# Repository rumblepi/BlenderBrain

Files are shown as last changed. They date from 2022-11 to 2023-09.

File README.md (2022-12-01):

# BlenderBrain

A controller for continuous flow blending of Nitrox and Trimix gases for diving.
The controller uses two oxygen sensors (one after Helium injection and one after Oxygen injection) and from this computes the composition of the resulting gas.
The desired mix can be adjusted by the user and is then automatically controlled via two magnetic valves. Depending on the currently measured mix, the valves are kept open longer or shorter. For this, a PI controller is implemented.

## Hardware

In the 'Hardware' folder, the KiCad files for the PCB are stored. Due to availability issues, the current configuration of the controller uses an Atmega168 microcontroller, but if available an Atmega328P can and should be used. The board requires two power supplies, one 5V to supply the microcontroller and operational amplifiers and a 24V to supply the magnetic valves as well as the indicator lights.

The oxygen sensors are assumed to be common rebreather sensors, namely ones similar to the NRC D-05R sensor range. These sensors expose three pins, of which we will use two to measure the output voltage. These galvanic cell sensors are dependent current sources outputting a given current for a certain oxygen partial pressure. The sensor also contains a small temperature compensation circuit with a few resistors and an NTC element, such that it effectively outputts a small voltage depending on the current oxygen partial pressure.
For more details see for example [http://www.advanceddivermagazine.com/articles/sensors/sensors.html].

As operational amplifiers, two TLC271 chips are used, but could be combined into a single TLC272 chip in the future. These OpAmps operate in non-inverting configuration with a gain of 101 and an additional feedback capacitor to filter high frequency noise. Note that only two of the three pins of the oxygen sensor are used.

### Programming the microcontroller via ISP

In-System-Programming can be used to update the firmware of the microcontroller. A detailed description of this procedure is given on the Arduino webpage (https://docs.arduino.cc/built-in-examples/arduino-isp/ArduinoISP), we store the most important points here for future reference.
We use an Arduino UNO in ISP mode to write to the Atmega microcontroller chip via the ISP pins on the board. 
Then, in the Arduino IDE the ISP sketch must be uploaded to the UNO via 'File->Examples->ArduinoISP->ArduinoISP'.

The ISP pins have a silkscreen overlay and the connections to the UNO are as follows: MOSI - 11, MISO - 12, SCK - 13, VCC - 5V, GND - GND, RESET - 10
In addition to this, it might be necessary to put a 10uF capacitor between the RESET and GND pins on the UNO.
The Atmega168 is available as processor of an Arduino Duemilanove, so in order to program it, select 'Tools->Board->Arduino Duemilanove or Dieciemila' and switch the processor to 'Atmega168' via 'Tools->Processor->Atmega168'. As we are using the UNO as an In-System-Programmer, also select 'Tools->Programmer->Arduino as ISP'. At first it might be necessary to burn a bootloader onto the chip, so select 'Tools->Burn Bootloader'. After that, the standard 'Upload'-button should do the trick.

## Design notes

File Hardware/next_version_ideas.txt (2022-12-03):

Possible hardware upgrades for the next version

Add hardware debounce circuits (Schmitt triggers and capacitors)
Fix holes for mounting the display
Add encoders to pcb
Fix footprints for button/etc adapters
Shrink overall footprint
Combine He/O2 op amp circuits
Combine two rotary encoders into one - switch gas by button push

Power supply?
SMT?

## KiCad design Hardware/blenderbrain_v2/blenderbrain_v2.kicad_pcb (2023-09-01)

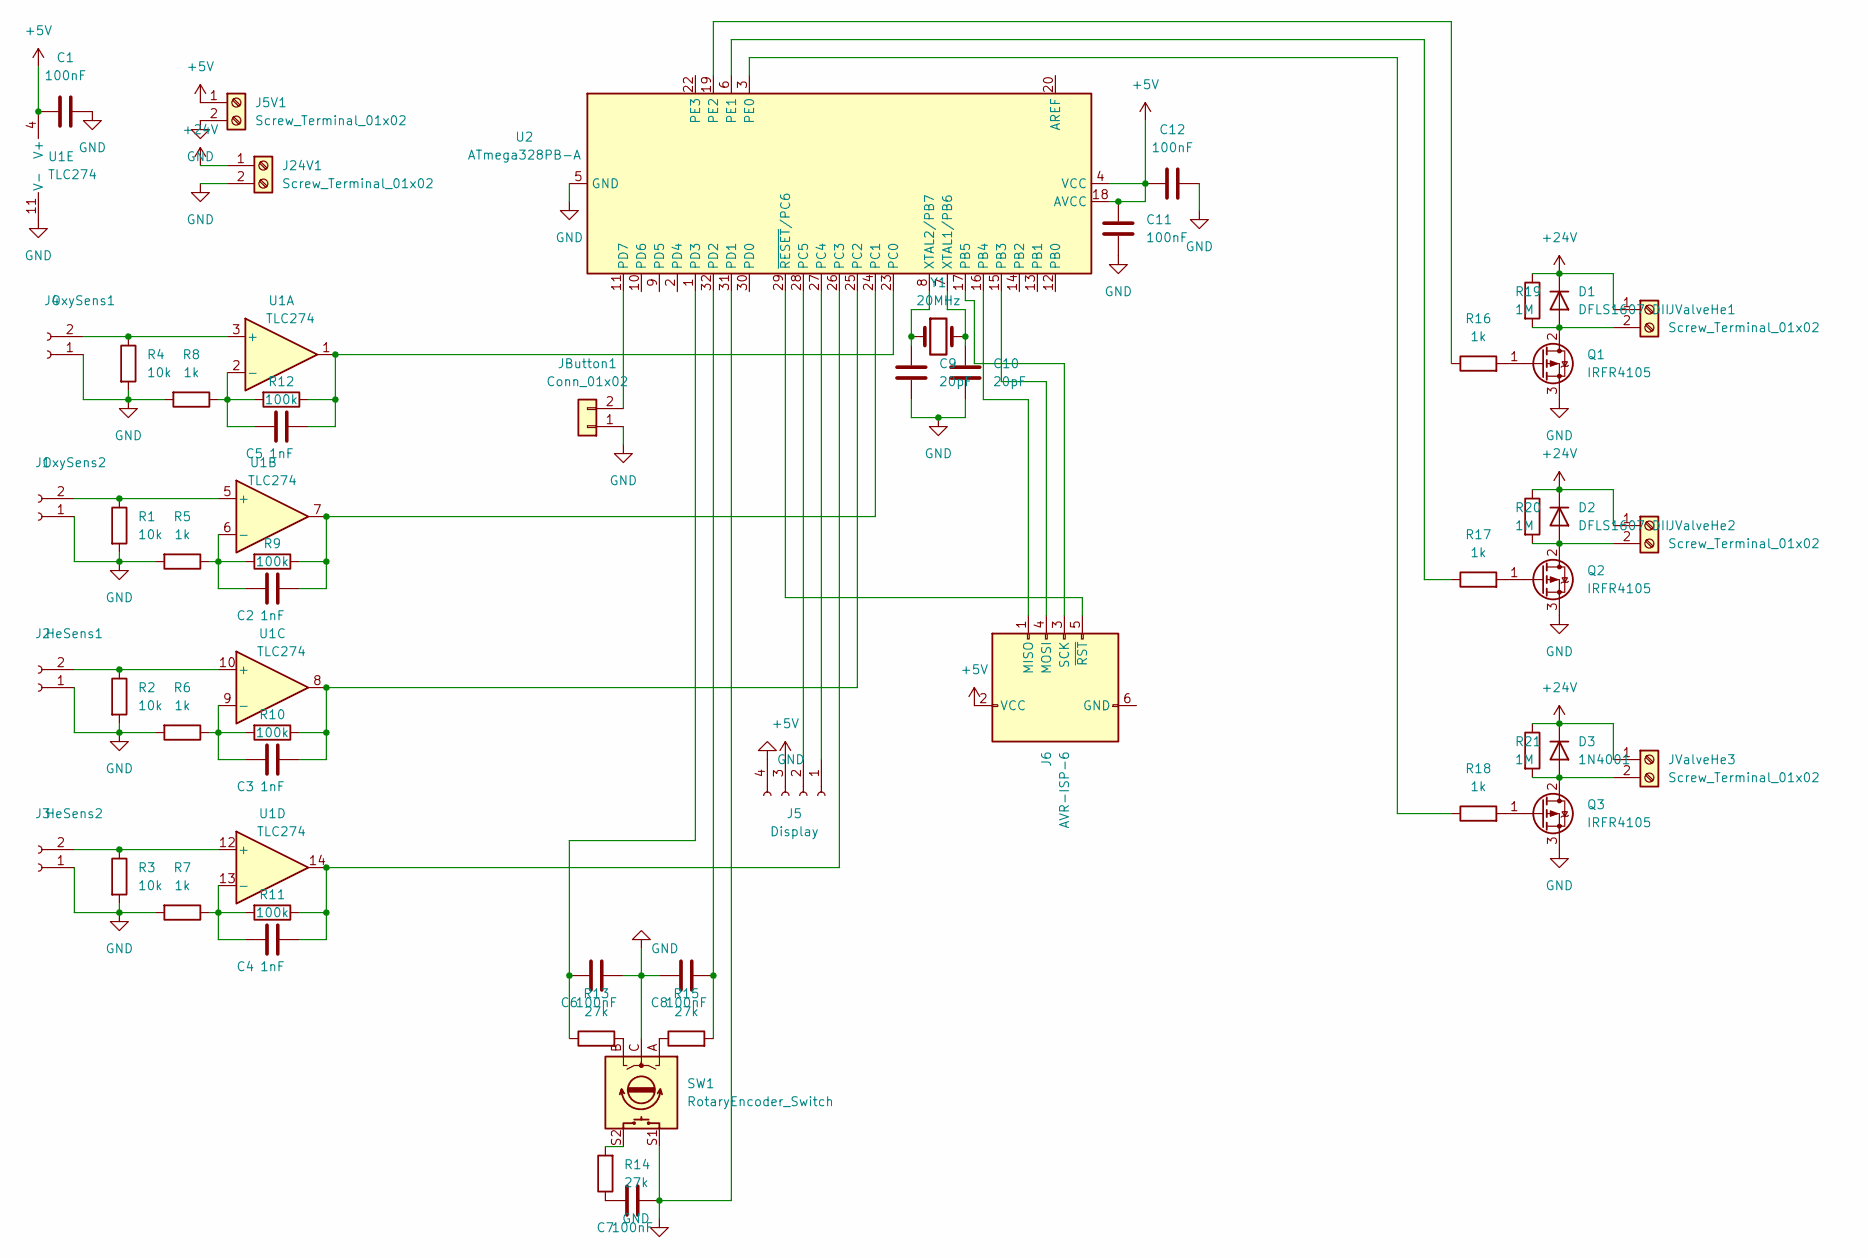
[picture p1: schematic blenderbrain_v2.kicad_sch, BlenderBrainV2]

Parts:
C1, C6, C7, C8, C11, C12: 100nF; C_1206_3216Metric
C2, C3, C4, C5: 1nF; C_1206_3216Metric
C9, C10: 20pF; C_1206_3216Metric
D1, D2: DFLS1607 DII; D_PowerDI-123
D3: 1N4001; D_PowerDI-123
J1: OxySens2; JST_EH_S2B-EH_1x02_P2.50mm_Horizontal
J2: HeSens1; JST_EH_S2B-EH_1x02_P2.50mm_Horizontal
J3: HeSens2; JST_EH_S2B-EH_1x02_P2.50mm_Horizontal
J4: OxySens1; JST_EH_S2B-EH_1x02_P2.50mm_Horizontal
J5: Display; PinSocket_1x04_P2.54mm_Vertical
J5V1, J24V1: Screw_Terminal_01x02; TerminalBlock_bornier-2_P5.08mm
J6: AVR-ISP-6; PinHeader_2x03_P2.54mm_Vertical
JButton1: Conn_01x02; PinHeader_1x02_P2.54mm_Vertical
JValveHe1, JValveHe2, JValveHe3: Screw_Terminal_01x02; JST_EH_B2B-EH-A_1x02_P2.50mm_Vertical
Q1, Q2, Q3: IRFR4105; TO-252-2
R1, R2, R3, R4: 10k; R_1206_3216Metric
R5, R6, R7, R8, R16, R17, R18: 1k; R_1206_3216Metric
R9, R10, R11, R12: 100k; R_1206_3216Metric
R13, R14, R15: 27k; R_1206_3216Metric
R19, R20, R21: 1M; R_1206_3216Metric
SW1: RotaryEncoder_Switch; RotaryEncoder_Alps_EC11E-Switch_Vertical_H20mm
U1: TLC274; SO-14_3.9x8.65mm_P1.27mm
U2: ATmega328PB-A; TQFP-32_7x7mm_P0.8mm
Y1: 20MHz; Crystal_HC49-U_Vertical

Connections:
+5V: C1.1, C11.2, C12.1, J5.3, J5V1.1, J6.2 (VCC), U1.4 (V+), U2.4 (VCC), U2.18 (AVCC)
+24V: D1.1 (K), D2.1 (K), D3.1 (K), J24V1.1, JValveHe1.1, JValveHe2.1, JValveHe3.1, R19.1, R20.1, R21.1
GND: C1.2, C6.2, C7.2, C8.1, C9.2, C10.2, C11.1, C12.2, J1.1, J2.1, J3.1, J4.1, J5.4, J5V1.2, J24V1.2, JButton1.1, Q1.3 (S), Q2.3 (S), Q3.3 (S), R1.2, R2.2, R3.2, R4.2, R5.2, R6.2, R7.2, R8.2, SW1.C, SW1.S1, U1.11 (V-), U2.5 (GND), U2.21 (GND), U2.31 (PD1)
unnamed: C2.1, R5.1, R9.2, U1.6 (-)
unnamed: C2.2, R9.1, U1.7, U2.24 (PC1)
unnamed: C3.1, R6.1, R10.2, U1.9 (-)
unnamed: C3.2, R10.1, U1.8, U2.25 (PC2)
unnamed: C4.1, R7.1, R11.2, U1.13 (-)
unnamed: C4.2, R11.1, U1.14, U2.26 (PC3)
unnamed: C5.1, R8.1, R12.2, U1.2 (-)
unnamed: C5.2, R12.1, U1.1, U2.23 (PC0)
unnamed: C6.1, R13.1, U2.1 (PD3)
unnamed: C7.1, R14.1
unnamed: C9.1, U2.8 (XTAL2/PB7), Y1.1
unnamed: C10.1, U2.7 (XTAL1/PB6), Y1.2
unnamed: D1.2 (A), JValveHe1.2, Q1.2 (D), R19.2
unnamed: D2.2 (A), JValveHe2.2, Q2.2 (D), R20.2
unnamed: D3.2 (A), JValveHe3.2, Q3.2 (D), R21.2
unnamed: J1.2, R1.1, U1.5 (+)
unnamed: J2.2, R2.1, U1.10 (+)
unnamed: J3.2, R3.1, U1.12 (+)
unnamed: J4.2, R4.1, U1.3 (+)
unnamed: J5.1, U2.27 (PC4)
unnamed: J5.2, U2.28 (PC5)
unnamed: J6.1 (MISO), U2.16 (PB4)
unnamed: J6.3 (SCK), U2.17 (PB5)
unnamed: J6.4 (MOSI), U2.15 (PB3)
unnamed: J6.5 (~RST), U2.29 (~RESET/PC6)
unnamed: Q1.1 (G), R16.2
unnamed: Q2.1 (G), R17.2
unnamed: Q3.1 (G), R18.2
unnamed: R13.2, SW1.B
unnamed: R14.2, SW1.S2
unnamed: R15.1, SW1.A
unnamed: R16.1, U2.19 (PE2)
unnamed: R17.1, U2.6 (PE1)
unnamed: R18.1, U2.3 (PE0)
unnamed: JButton1.2, U2.11 (PD7)
unnamed: C8.2, R15.2, U2.32 (PD2)

Board: 2 copper layers, 55 parts (0 on the bottom side), 39 nets, no tracks yet.

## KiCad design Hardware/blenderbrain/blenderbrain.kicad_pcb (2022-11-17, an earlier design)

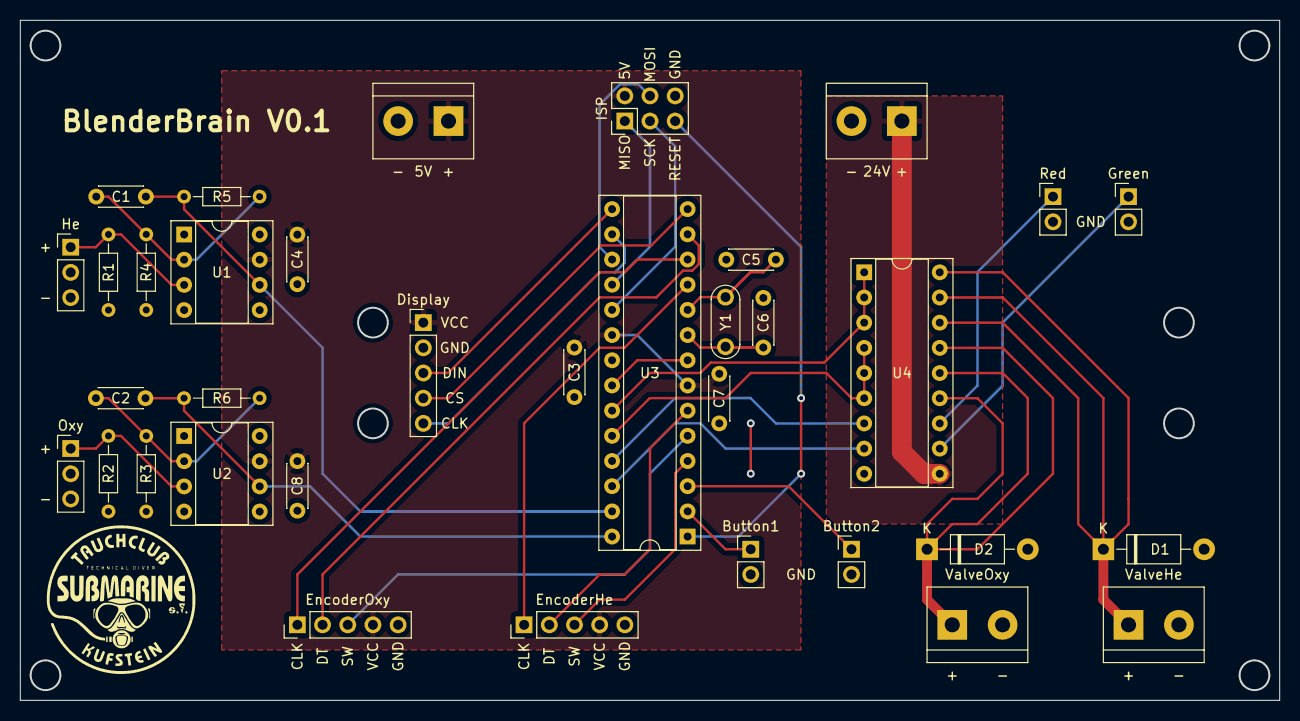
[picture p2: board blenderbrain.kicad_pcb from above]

Board: 2 copper layers, 127.0 x 68.6 mm, 35 parts (0 on the bottom side), 34 nets.

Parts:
5V, 24V: Screw_Terminal_01x02; TerminalBlock_bornier-2_P5.08mm
Button1, Button2: Conn_01x02; PinHeader_1x02_P2.54mm_Vertical
C1, C2: 1nF; C_Disc_D4.3mm_W1.9mm_P5.00mm
C3, C4, C7, C8: 100nF; C_Disc_D4.3mm_W1.9mm_P5.00mm
C5, C6: 20pF; C_Disc_D4.3mm_W1.9mm_P5.00mm
D1, D2: 1N4001; D_DO-41_SOD81_P10.16mm_Horizontal
Display: Conn_01x05_Male; PinHeader_1x05_P2.54mm_Vertical
EncoderHe: Conn_01x05_Male; PinHeader_1x05_P2.54mm_Vertical
EncoderOxy: Conn_01x05_Male; PinHeader_1x05_P2.54mm_Vertical
Green: Conn_01x02; PinHeader_1x02_P2.54mm_Vertical
He: Conn_He; PinHeader_1x03_P2.54mm_Vertical
ISP: AVR-ISP-6; PinHeader_2x03_P2.54mm_Vertical
Oxy: Conn_Oxy; PinHeader_1x03_P2.54mm_Vertical
R1, R2: 10k; R_Axial_DIN0204_L3.6mm_D1.6mm_P7.62mm_Horizontal
R3, R4: 1k; R_Axial_DIN0204_L3.6mm_D1.6mm_P7.62mm_Horizontal
R5, R6: 100k; R_Axial_DIN0204_L3.6mm_D1.6mm_P7.62mm_Horizontal
Red: Conn_01x02; PinHeader_1x02_P2.54mm_Vertical
U1, U2: OP177GPZ; DIP-8_W7.62mm_Socket
U3: ATmega168-20P; DIP-28_W7.62mm_Socket
U4: ULN2803A; DIP-18_W7.62mm_Socket
ValveHe: Screw_Terminal_01x02; TerminalBlock_bornier-2_P5.08mm
ValveOxy: Screw_Terminal_01x02; TerminalBlock_bornier-2_P5.08mm
Y1: 10MHz; Resonator-2Pin_W7.0mm_H2.5mm

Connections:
+5V: 5V.1, C3.1, C4.1, C7.2, C8.1, Display.1, EncoderHe.4, EncoderOxy.4, ISP.2 (VCC), U1.7 (V+), U2.7 (V+), U3.7 (VCC), U3.20 (AVCC)
+24V: 24V.1, U4.10 (COM)
GND: 5V.2, 24V.2, Button1.2, Button2.2, C3.2, C4.2, C5.2, C6.2, C7.1, C8.2, D1.2 (A), D2.2 (A), Display.2, EncoderHe.5, EncoderOxy.5, Green.2, He.3, ISP.6 (GND), Oxy.3, R1.2, R2.2, R3.2, R4.2, Red.2, U1.4 (V-), U2.4 (V-), U3.8 (GND), U3.22 (GND), U4.9 (GND), ValveHe.2, ValveOxy.2
unnamed: C1.1, R4.1, R5.2, U1.2 (-IN)
unnamed: C1.2, R5.1, U1.6 (OUT), U3.27 (PC4)
unnamed: C2.1, R3.1, R6.2, U2.2 (-IN)
unnamed: C2.2, R6.1, U2.6 (OUT), U3.28 (PC5)
unnamed: C5.1, U3.10 (XTAL2/PB7), Y1.1
unnamed: C6.1, U3.9 (XTAL1/PB6), Y1.2
unnamed: D1.1 (K), U4.16 (O3), U4.17 (O2), U4.18 (O1), ValveHe.1
unnamed: D2.1 (K), U4.13 (O6), U4.14 (O5), U4.15 (O4), ValveOxy.1
unnamed: He.1, R1.1, U1.3 (+IN)
unnamed: Oxy.1, R2.1, U2.3 (+IN)
unnamed: ISP.1 (MISO), U3.18 (PB4)
unnamed: ISP.3 (SCK), U3.19 (PB5)
unnamed: ISP.4 (MOSI), U3.17 (PB3)
unnamed: ISP.5 (~RST), U3.1 (~RESET/PC6)
unnamed: Button1.1, U3.2 (PD0)
unnamed: Button2.1, U3.3 (PD1)
unnamed: Display.3, U3.15 (PB1)
unnamed: Display.4, U3.14 (PB0)
unnamed: Display.5, U3.16 (PB2)
unnamed: EncoderHe.1, U3.11 (PD5)
unnamed: EncoderHe.2, U3.6 (PD4)
unnamed: EncoderHe.3, U3.4 (PD2)
unnamed: EncoderOxy.1, U3.12 (PD6)
unnamed: EncoderOxy.2, U3.13 (PD7)
unnamed: EncoderOxy.3, U3.5 (PD3)
unnamed: Green.1, U4.11 (O8)
unnamed: Red.1, U4.12 (O7)
unnamed: U3.23 (PC0), U4.1 (I1), U4.2 (I2), U4.3 (I3)
unnamed: U3.24 (PC1), U4.4 (I4), U4.5 (I5), U4.6 (I6)
unnamed: U3.25 (PC2), U4.7 (I7)
unnamed: U3.26 (PC3), U4.8 (I8)

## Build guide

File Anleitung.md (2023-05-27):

# Dokumentation: BlenderBrain Mischstation

Eine kurze Anleitung zur Bedienung der Mischanlage, sowie eine Checklist für alle Gasblender, die mit dem CF-Mischen vertraut sind.

## Aufbau und Funktion

Die BlenderBrain Mischstation ist eine continuous flow (CF) Mischanlage, mit der Sauerstoffmischungen bis 36%, sowie beliebige Trimixmischungen gemischt werden können. 

### Anschluss und Inbetriebnahme
Um die Mischstation in Betrieb zu nehmen müssen an die mit O2 und He markierten Ventile 6mm Pneumatikschläuche mit den entsprechenden Gasen und die Kompressoransaugung an das untere Ende des Mischrohrs angeschlossen werden. Weiters wird eine 5V Stromversorgung für den Controller benötigt, aktuell ist hierfür ein microUSB Anschluss verlötet, an den ein entsprechendes Ladekabel angeschlossen werden kann.

### Messprinzip
Die Messung basiert auf zwei in den Mischrohren angebrachten galvanischen Sauerstoffsensoren, die jeweils am Ende der Mischstrecke für ein Gas platziert sind. 
Zuerst wird Helium in das Ansaugrohr injiziert, vermischt sich im ersten Mischrohr mit der angesaugten Luft und diese Gasmischung wird dann vom ersten Sauerstoffsensor gemessen. 
Der Sensor detektiert den verminderten Sauerstoffpartialdruck und kann dadurch auf die enthaltene Heliummenge rückrechnen. 
Als Zweites wird der Sauerstoff eingebracht und vermischt sich im zweiten Mischrohr mit dem vorherigen Gasgemisch. Im zweiten Sauerstoffsensor wird der finale Sauerstoffgehalt der Mischung bestimmt.

### Gasinjektion
Im aktuellen Ausbau erfolgt die Gasinjektion von Helium und Sauerstoff manuell durch den Gasblender über Drosselrückschlagventile. 
Ein Ausbau auf eine automatische Mischanlage mit Magnetventilen ist aktuell in Planung.

***Der Gasblender muss dafür sorge tragen, dass NIEMALS im Betrieb der Sauerstoffgehalt der Mischung 40% übersteigt! Es sind keine Sicherheitsmechanismen verbaut, die eine eventuelle Explosion verhindern können.***

### Anzeige und Einstellung
Das Menü ist linear aufgebaut, die Anzeige erfolgt auf acht Siebensegmentanzeigen.

Es gibt zwei Betriebsmodi: *Einstellen* und *Mischvorgang*

#### Einstellen
Im Einstellungsmenü steht auf der linken Seite immer die Bezeichnung der aktuellen Einstellung, auf der rechten Seite steht der Wert.
Die möglichen Größen, die vom Bediener eingestellt werden können sind (in dieser Reihenfolge)

- 'P  0': der aktuelle Druck in der Flasche
- 'He 0': der aktuelle Heliumgehalt in der Flasche
- 'O2 0': der aktuelle Sauerstoffgehalt in der Flasche
- 'P  1': der gewünschte Druck in der Flasche
- 'He 1': der gewünschte Heliumgehalt in der Flasche
- 'O2 1': der gewünschte Sauerstoffgehalt in der Flasche

Die Werte können hierbei immer mit dem Encoder eingestellt werden, die Bestätigung erfolgt durch Druck auf den Encoder (*nicht* auf den Knopf daneben, siehe unten).
Im Anschluss erscheint 'Go' auf dem Display, wenn man hier Bestätigt wird der Mischvorgang gestartet.
Falls sich doch ein Fehler eingeschlichen hat, kann das Menü durch Druck auf den rechten Knopf zurückgesetzt werden, die bereits erfolgten Einstellungen bleiben dabei gespeichert und die Sensoren werden neu kalibriert.

#### Mischvorgang
Während des Mischvorgangs ändert sich die Darstellung auf acht Zahlen, diese sind in vier Blöcke gruppiert:

|O2 Soll|He Soll|O2 Ist|He Ist|

Die Aufgabe des Gasblenders ist es jetzt O2Soll und O2Ist, sowie HeSoll und HeIst so gut wie möglich zur Übereinstimmung zu bringen.
Das erfolgt durch dosiertes öffnen und schließen der Drosselrückschlagventile. 

**Mit dem Sauerstoffventil sehr vorsichtig umgehen, da sonst schnell eine explosive Mischung im Kompressor entstehen kann**

Ein Beispiel: Die eingestellte Mischung ist 21/35, es wird aber Luft angesaugt. Dann wird am Anfang 

|21|35|21|00|

angezeigt. Diese Anzeige wird sich aber schnell auf

|21|99|21|00| 

ändern, da der Controller aktiv versucht dem Bediener klarzumachen, dass mehr Helium nachgeregelt werden muss.
Der Bediener erkennt das und öffnet das Heliumventil etwas, sodass keine reine Luft mehr angesaugt wird. Die Anzeige
ändert sich (zum Beispiel) auf

|40|50|16|20|.

Jetzt muss der Bediener sowohl Helium als auch Sauerstoff nachregeln (der Controller sollte nie mehr als 40% Sauerstoff verlangen - falls doch bitte **NICHT** daran halten, sondern immer unter 40% bleiben und den Fehler an Michael Sandbichler melden)
Kontrolliertes Regeln der Ventile führt dann irgendwann zu einer Stabilisierung der Anzeige, die aber nicht unbedingt der eingestellten Mischung entsprechen muss.
Die geforderte Mischung hängt von der Mischung in der Flasche, der gewünschten Mischung und dem Verlauf des Mischvorgangs ab.
Es könnte sich zum Beispiel auf

|24|33|24|33|

einpendeln.

**Achtung: Wenn jetzt der Reset-Knopf betätigt wird, dann werden die Sensoren auf 21|00 kalibriert - was aber nicht der aktuellen Mischung im Mischrohr entspricht. 
Daher vor Reset immer das Mischrohr mit Luft spülen oder (wenn schon resettet wurde) nach der Luftspülung noch ein weiteres mal resetten.**

# Checkliste

- Kompressor ausschalten
- Speicherflaschen schließen
- Druck aus Kompressor und Rohren ablassen
- Kompressoransaugung an Mischanlage anschließen
- Mischung und Druck der Flasche, in die gemischt werden soll messen
- Flasche an die Füllarmatur anschließen
- Sauerstoff- und Heliumspeicherflasche öffnen und Anschlüsse prüfen
- BlenderBrain einschalten
- Bei 'P  0', 'O2 0' und 'He 0' den aktuellen Flaschendruck, Sauerstoff- und Heliumgehalt einstellen
- Bei 'P  1', 'O2 1' und 'He 1' den gewünschten Flaschendruck, Sauerstoff- und Heliumgehalt einstellen
- Ungefähr gleichzeitig 'Go' am BlenderBrain aktivieren und den Kompressor einschalten
- Helium- und Sauerstoffgehalt mit den Ventilen einregeln. 

***Sauerstoff darf NIE über 40% sein - EXPLOSIONSGEFAHR!***

Wenn die Mischung fertig ist:
- Ventile schließen
- Kompressor ausschalten
- Flasche von Füllarmatur abschließen
- Sauerstoff- und Heliumspeicherflasche schließen
- Kompressoransaugung wieder ans normale Ansaugrohr anschließen
- Druck aus Kompressor und Rohren ablassen ***Wichtig - die nächsten messen vermutlich nicht nach!***
- Speicherflaschen öffnen

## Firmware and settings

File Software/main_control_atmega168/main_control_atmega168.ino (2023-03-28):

/*
 Main Control
 This file contains the main control logic uploaded to the Atmega168 for gas blending using the BlenderBrain control
 (c) Nov 17, 2022 Michael Sandbichler
*/
#include "LedControl.h"

//#define DEBUGMODE
///////////////////////////////////////////////////////////////////
// Pins etc

// Define all pins and objects according to the schematic 
// given in the 'Hardware' folder
// `* Sensors and Actuators
#define OXY_SENSOR_PIN A5
#define HE_SENSOR_PIN A4
#define HE_VALVE_PIN A0
#define OXY_VALVE_PIN A1

#define BUTTON1_PIN 0
#define BUTTON2_PIN 1
#define RED_LIGHT_PIN A2
#define GREEN_LIGHT_PIN A3

#define DISPLAY_DIN_PIN 9
#define DISPLAY_CS_PIN 8
#define DISPLAY_CLK_PIN 10

//* Encoders
#define OXY_ENCODER_CLK 6
#define OXY_ENCODER_DT 7
#define OXY_ENCODER_SW 3
#define HE_ENCODER_CLK 5
#define HE_ENCODER_DT 4
#define HE_ENCODER_SW 2

//* Other fixed numbers
float VALVE_PWM_PERIOD_MS = 1000;

//* Global variables
float oxySetPoint = 21.5;
int oldClockOxy = -1; 
bool oxyFixed = false;

float heSetPoint = 0.5;
int oldClockHe = -1;
bool heFixed = false;

float oxySensorCalib = 0;
float oxySensorValue = 20.95;
float lastOxyValue = 20.95;

enum MachineState{
  //! The MachineState guides through the main loop and switches on the respective functions
  MixSetting,
  SettingComplete,
  MixActive,
};

enum ErrorCode {
  //! Exit codes for different errors
  ImpossibleMix  
};

enum MixMode{
  //! For Nitrox and Heliox only one valve is on, for Trimix both valves inject gas
  Nitrox,
  Heliox,
  Trimix
};

enum GasType{
  Helium,
  Oxygen
};

// The starting state is the 'MixSetting'
MachineState currentState = MachineState::MixSetting;

enum ButtonState{
  Down,
  Up  
};

//! Clip a given floating point number to a minimum and maximum value
float clip(float number, float min, float max) {
  if (number < min) return min;
  if (number > max) return max;
  return number;  
}

/*! The Debouncer object can be used to wait a fixed time after an event
 *  while still continuing with all tasks (i.e. without having to use a
 *  delay() method)
 */
struct Debouncer {
  Debouncer(float delay):
    delay_(delay),
    lastDebounce_(0){}

  //! returns true if the delay has elapsed since the last call
  bool check() {
    if(millis() - lastDebounce_ > delay_) {
      lastDebounce_ = millis();
      return true;
    }
    return false;
  }
  
  float delay_;
  long lastDebounce_;
};

/*! The DebouncedButton makes use of the Debouncer class to 
 * stabilize bouncing button pushes
 */
struct DebouncedButton {
  Debouncer debounce_ = Debouncer(0.05);

  DebouncedButton(int pin, long time = 0) :
    pin_(pin),
    currentState_(ButtonState::Up)    
  {}

  //! Returns +1 if the button changed from 'Down' to 'Up', -1 if the button changed from
  //! 'Up' to 'Down' and 0 if the state did not change.
  int stateChanged() {
      if(debounce_.check()){
        ButtonState pinState = digitalRead(pin_)? ButtonState::Up : ButtonState::Down;
        if (pinState == ButtonState::Down && currentState_== ButtonState::Up) {
          currentState_ = pinState;
          return 1;
        } else if (pinState == ButtonState::Up && currentState_== ButtonState::Down) {
          currentState_ = pinState;
          return -1; 
        } else {
          return 0;
        }
      }
      return 0;
  }   

  int pin_;
  ButtonState currentState_;
};

DebouncedButton heEncoderButton(HE_ENCODER_SW);
DebouncedButton oxyEncoderButton(OXY_ENCODER_SW);
DebouncedButton startButton(BUTTON1_PIN);
DebouncedButton endButton(BUTTON2_PIN);

//! Implements proportional-integral control to adjust a quantity to a certain target value
//! This controller clips the outputs to the interval [0,1]
struct PIControl {
  double targetValue_;
  double Kp_, Ki_;
  
  unsigned long prevUpdateTime_;
  double prevError_, intError_;
  short saturation_; //the controller operates in the saturation region

  PIControl(double targetValue, double Kp, double Ki) :
    targetValue_(targetValue),
    Kp_(Kp),
    Ki_(Ki),
    prevUpdateTime_(0),
    intError_(0),
    saturation_(0){}
  
  double clipToUnitInterval(double const & x) {
    if (x < 0) {
      saturation_ = -1;
      return 0;
    }
    if (x > 1) {
      saturation_= 1;
      return 1;
    }
    saturation_= 0;
    return x;
  }

  double compute(double inputValue) {
    long currentTime = millis();
    double elapsed = (double) (currentTime - prevUpdateTime_);
    double error = targetValue_ - inputValue;
    if((saturation_ > 0 && error > 0) || (saturation_ < 0 && error < 0)) {
      //skip if saturation and error are in the same direction
    } else {
      intError_ += Ki_*error*elapsed;
    }
    intError_ = clipToUnitInterval(intError_);
    double out = clipToUnitInterval(Kp_*error + intError_);
    prevUpdateTime_ = currentTime;        
    return out;
  }  
};

PIControl oxyControl(20.95,0.01,0.001);
PIControl heControl(0.0,0.01,0.001);

struct MagneticValve {
  int pin_;
  float s_;//fraction of the pwm period to switch the valve on
  bool on_;
  MagneticValve(int pin):
    pin_(pin),
    s_(1),
    on_(false){}    

  Debouncer pwmPeriod_ = Debouncer(VALVE_PWM_PERIOD_MS);
  Debouncer onPeriod_ = Debouncer(s_*VALVE_PWM_PERIOD_MS);

  void switchOn() {
    digitalWrite(pin_, true);
    on_ = true;
  }

  void switchOff() {
    digitalWrite(pin_, false);
    on_ = false;
  }

  void setS(float newS) {
    if(newS >= 1 or newS <= 0){
      return;
    } 
    s_ = newS;
    onPeriod_.delay_=s_*VALVE_PWM_PERIOD_MS;  
  }
  
  void update() {
    if(!pwmPeriod_.check() &&  onPeriod_.check()) {
      if(!on_){
        return;
      } else {
        switchOff();
        return;
      }
    }
    if(!on_){
      switchOn();
    }
    return;
  }
};

struct StatusLed {
  enum LedState {
    On,
    Off,
    Blinking
  };
  int pin_;
  LedState status_;
  Debouncer blinker_ = Debouncer(1000);
  Debouncer secondBlink_ = Debouncer(500);

  StatusLed(int pin):
    pin_(pin),
    status_(LedState::Off) {}
  
  void update(){
    switch(status_) {
      case LedState::On:
        digitalWrite(pin_, true);
        break;
      case LedState::Off:
        digitalWrite(pin_, false);
        break;
      case LedState::Blinking:
        if (!blinker_.check() && !secondBlink_.check()){
            digitalWrite(pin_,true);
          } else {
            digitalWrite(pin_,false);
          }
        break;
    }
  }
};

StatusLed redLed(RED_LIGHT_PIN);
StatusLed greenLed(GREEN_LIGHT_PIN);

struct EightDigitDisplay {
  LedControl lc_;
  EightDigitDisplay(LedControl lc) :
    lc_(lc) {
      lc_.shutdown(0,false);
      /* Set the brightness to a medium values */
      lc_.setIntensity(0,2);
      /* and clear the display */
      lc_.clearDisplay(0);      
  }

  void clear() {
    lc_.clearDisplay(0);
  }  

  void writeNumber(int number) {
    // Writes the first eight digits of a given number to the display
    for(int i=0; i<8; ++i) {
      lc_.setDigit(0,i,(number/((int) pow(10,i))) % 10,false);
    }
  }
  
  void writePreText(char* txt) {
    //The length of txt must not be larger than four characters and will be displayed
    for(int i = 0; i < 4; ++i) {
      lc_.setChar(0,7-i,txt[i],false);
      if(txt[i]=='t'){
        lc_.setLed(0,7-i,4,true);  
        lc_.setLed(0,7-i,5,true);  
        lc_.setLed(0,7-i,6,true);  
        lc_.setLed(0,7-i,7,true);       
        }
      if(txt[i]=='S'){
        lc_.setDigit(0,7-i,5,false);
      }
    }
  }

  void writeFullText(char* txt) {
    //The length of txt must not be larger than eight characters and will be displayed
    for(int i = 0; i < 8; ++i) {
      lc_.setChar(0,7-i,txt[i],false);
      if(txt[i]=='t'){
        lc_.setLed(0,7-i,4,true);  
        lc_.setLed(0,7-i,5,true);  
        lc_.setLed(0,7-i,6,true);  
        lc_.setLed(0,7-i,7,true);       
        }
      if(txt[i]=='S'){
        lc_.setDigit(0,7-i,5,false);
      }
    }
  }
  void writeTwoDigits(int number, int pos) {
    //write two digits at position 1,2,3 or 4 of the display |11|22|33|44|
    lc_.setDigit(0,7-2*(pos-1),(number/10) % 10,false);
    lc_.setDigit(0,6-2*(pos-1),number % 10,false);
  }

};

EightDigitDisplay display(LedControl(DISPLAY_DIN_PIN,DISPLAY_CLK_PIN,DISPLAY_CS_PIN,1));

struct Sensor {
  Sensor(int pin, float calibValue):
    pin_(pin)
    {
      lastValue_ = calibValue;
      calibration_ = calibValue/measureAverage(30);
    }

  void recalibrate(float calibValue) {
      calibration_ = calibValue/measureAverage(30);
  }

  float measureAverage(int num) {
    float output = 0;
    for(int i = 0; i < num; ++i) {
      output += analogRead(pin_);
    }
    return output /(float)num;
  }
  
  void update() {
    lastValue_ = clip(measureAverage(20)*calibration_, 0,99);
  }
    
  void display(EightDigitDisplay display, int pos) {
    display.writeTwoDigits((int) round(lastValue_), pos);
  }

  int pin_;
  float calibration_;
  float lastValue_;
};

struct Setpoint {
  Debouncer displayDebounce_ = Debouncer(0.1);

  Setpoint(float oxy = 20.95, float he = 0.0) :
    hePercent_(he),
    oxyPercent_(oxy),
    minOxy_(0),
    maxOxy_(100.0){}  

  void setHePercent(float newHe) {
    hePercent_ = clip(newHe,0,99);
    minOxy_ = 20.95*(1-hePercent_/100.);
  }
  
  void setOxyPercent(float newOxy) {
    oxyPercent_ = clip(newOxy, minOxy_, maxOxy_);
  }

  void computeFromSensors(Sensor oxySensor, Sensor heSensor) {
    oxyPercent_ = oxySensor.lastValue_;
    hePercent_ = 100*(1-heSensor.lastValue_/21)*(1-(oxySensor.lastValue_-heSensor.lastValue_)/(100-heSensor.lastValue_));
  }

  float computeHeSensorValue() {
    return 100 - 79.05*(100-oxyPercent_)/(100-oxyPercent_-0.2095*hePercent_);
  }
  
  void display(EightDigitDisplay & display, int pos) {
    if(!displayDebounce_.check())return;
    //draw at position 0 or 1 [0000|1111]
    switch(pos){
      case 0:
        display.writeTwoDigits(round(oxyPercent_), 1);
        display.writeTwoDigits(round(hePercent_), 2);
        break;
      case 1:
        display.writeTwoDigits(round(oxyPercent_), 3);
        display.writeTwoDigits(round(hePercent_), 4);
        break;
      default:
        return;     
    }
  }  
  float hePercent_;
  float oxyPercent_;
  float minOxy_, maxOxy_;
};

Setpoint currentPercent;
Setpoint wantedPercent;

struct ButtonEncoder {
  ButtonEncoder(int clkPin, int dtPin, int buttonPin):
    clk_(clkPin),
    dt_(dtPin),
    state_(0),
    fixed_(false),
    button_(DebouncedButton(buttonPin)){}

  void read(float & setpoint) {
    bool clockVal = digitalRead(clk_);
    bool dataVal = digitalRead(dt_);
    switch (state_) {
        case 0:                         // Idle state, encoder not turning
            if (!clockVal){             // Turn clockwise and CLK goes low first
                state_ = 1;
            } else if (!dataVal) {      // Turn anticlockwise and DT goes low first
                state_ = 4;
            }
            break;
        // Clockwise rotation
        case 1:                     
            if (!dataVal) {             // Continue clockwise and DT will go low after CLK
                state_ = 2;
            } 
            break;
        case 2:
            if (clockVal) {             // Turn further and CLK will go high first
                state_ = 3;
            }
            break;
        case 3:
            if (clockVal && dataVal) {  // Both CLK and DT now high as the encoder completes one step clockwise
                state_ = 0;
                ++setpoint;
            }
            break;
        // Anticlockwise rotation
        case 4:                         // As for clockwise but with CLK and DT reversed
            if (!clockVal) {
                state_ = 5;
            }
            break;
        case 5:
            if (dataVal) {
                state_ = 6;
            }
            break;
        case 6:
            if (clockVal && dataVal) {
                state_ = 0;
                --setpoint;
            }
            break; 
    }
  }


  void updateSetpoint(Setpoint & sp, GasType gas) {
    float currSp;
    switch(gas) {
      case GasType::Helium:
        currSp = sp.hePercent_;
        read(currSp);
        sp.setHePercent(currSp);
        break;
      case GasType::Oxygen:
        currSp = sp.oxyPercent_;
        read(currSp);
        sp.setOxyPercent(currSp);
        break;
      default:
        return;
    }
  }

  int clk_, dt_;
  bool fixed_;
  unsigned int state_;
  DebouncedButton button_;
};

ButtonEncoder oxyEncoder(OXY_ENCODER_CLK, OXY_ENCODER_DT, OXY_ENCODER_SW);
ButtonEncoder heEncoder(HE_ENCODER_CLK, HE_ENCODER_DT, HE_ENCODER_SW);

Sensor oxySensor(OXY_SENSOR_PIN, 20.95);
Sensor heSensor(HE_SENSOR_PIN, 20.95);

#ifdef DEBUGMODE
void debugDisplay() {
    float sensorVal = heSensor.measureAverage(20);
    //if (oxySensorValue - lastOxyValue > 1 || oxySensorValue - lastOxyValue < -1) {
    display.writeNumber(sensorVal); //update display
    //} 
}
#endif

//////////////////////////////////////////////////////////////////
// Basic microcontroller methods

//TODO rebuild with new objects

void setup() {  
  Serial.begin(9600); 
  pinMode(OXY_SENSOR_PIN, INPUT);
  pinMode(HE_SENSOR_PIN, INPUT);

  pinMode(OXY_VALVE_PIN, OUTPUT);
  pinMode(HE_VALVE_PIN, OUTPUT);

  pinMode(HE_ENCODER_SW, INPUT_PULLUP);
  pinMode(OXY_ENCODER_SW, INPUT_PULLUP);


  wantedPercent.minOxy_ = 20.95;
  wantedPercent.maxOxy_ = 40.0;
  delay(1000);
  oxySensor.recalibrate(20.95);
  heSensor.recalibrate(20.95);
  currentPercent.displayDebounce_.delay_ = 100;
}

void loop() {
#ifdef DEBUGMODE
  debugDisplay();
  delay(1000);
#else
  switch(currentState) {
    case MachineState::MixSetting:
      heEncoder.updateSetpoint(wantedPercent, GasType::Helium);
      oxyEncoder.updateSetpoint(wantedPercent, GasType::Oxygen);
      oxySensor.update();
      heSensor.update();
      currentPercent.computeFromSensors(oxySensor, heSensor);
      break;      
    case MachineState::MixActive:
      oxySensor.update();
      heSensor.update();
      currentPercent.computeFromSensors(oxySensor, heSensor);
      break;
    default:
      break;    
  }

  wantedPercent.display(display, 0);
  currentPercent.display(display,1);
#endif
}

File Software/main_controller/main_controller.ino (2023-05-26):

/*
 Main Control
 This file contains the main control logic uploaded to the Atmega168 for gas blending using the BlenderBrain control
 (c) Mar 28, 2023 Michael Sandbichler
*/
///////////////////////////////////////////////////////////////////
// Pins etc
#include "BasicStructures.hpp"
#include "UI.hpp"
#include "Encoder.hpp"
#include "Sensor.hpp"
#include "Display.hpp"
#include "Setpoint.hpp"

// Define all pins and objects according to the schematic 
// given in the 'Hardware' folder
// `* Sensors and Actuators
#define OXY_SENSOR_PIN A5
#define HE_SENSOR_PIN A4
#define HE_VALVE_PIN A0
#define OXY_VALVE_PIN A1

#define RED_LIGHT_PIN A2
#define GREEN_LIGHT_PIN A3

#define DISPLAY_DIN_PIN 9
#define DISPLAY_CS_PIN 8
#define DISPLAY_CLK_PIN 10

#define RESET_BUTTON_PIN 0

//* Encoders
#define ENCODER_CLK 6
#define ENCODER_DT 7
#define ENCODER_SW 3

enum ErrorCode {
  //! Exit codes for different errors
  ImpossibleMix  
};

enum MixMode{
  //! For Nitrox and Heliox only one valve is on, for Trimix both valves inject gas
  Nitrox,
  Heliox,
  Trimix
};

struct MixSetup {
  bool
  updateFromMixMenu(MixMenu settings) {
    pressureBefore = settings.pPrev.value();
    pressureAfter = settings.pPost.value();
    mixBefore = Setpoint(settings.o2Prev.value(), settings.hePrev.value());
    mixAfter = Setpoint(settings.o2Post.value(), settings.hePost.value());
    integralControlMix.oxyPercent_.maximum(40.0);
    return computeRequiredMix();
  }

  bool 
  computeRequiredMix() {
    float prevFraction = static_cast<float>(pressureBefore) / pressureAfter;
    float requiredHe = (mixAfter.hePercent_.get() - prevFraction*mixBefore.hePercent_.get())/(1-prevFraction);
    float requiredO2 = (mixAfter.oxyPercent_.get() - prevFraction*mixBefore.oxyPercent_.get())/(1-prevFraction);
    if (requiredO2 > 40 || requiredO2 < 0 || requiredHe < 0 || requiredHe > 100) {
      return false;
    }
    mixRequired = Setpoint(requiredO2, requiredHe);
    mixEstimated = Setpoint(20.95, 0);
    updateIntegralControl();
    prevTime_ = millis();
    return true;
  }

  bool
  updateEstimatedMix(Setpoint measuredMix) {
    if(!integralDebouncer.check()) return false;
    float now = millis();
    float dt = now - prevTime_;
    mixEstimated.setOxyPercent((mixEstimated.oxyPercent_.get()*elapsedTime_ + measuredMix.oxyPercent_.get()*dt)/(elapsedTime_ + dt));
    mixEstimated.setHePercent((mixEstimated.hePercent_.get()*elapsedTime_ + measuredMix.hePercent_.get()*dt)/(elapsedTime_ + dt));
    elapsedTime_ = elapsedTime_ + dt;
    prevTime_ = now;
    return true;
  }

  void
  resetEstimatedMix() {
    mixEstimated = Setpoint(20.95, 0);
    elapsedTime_ = 0;
  }

  bool 
  updateIntegralControl() {
    integralControlMix.setOxyPercent(2*mixRequired.oxyPercent_.get() - mixEstimated.oxyPercent_.get());
    integralControlMix.setHePercent(2*mixRequired.hePercent_.get() - mixEstimated.hePercent_.get());
    return true;
  }

  int pressureBefore;
  int pressureAfter;
  Setpoint mixBefore;
  Setpoint mixAfter; 
  Setpoint mixRequired;
  Setpoint mixEstimated;
  Debouncer integralDebouncer = Debouncer(500);
  float prevTime_ = 0;
  float elapsedTime_ = 0;

  Setpoint integralControlMix;

};

///////////////////////////////////////////////////////////////////

ButtonEncoder encoder = ButtonEncoder(ENCODER_CLK, ENCODER_DT, ENCODER_SW);
DebouncedButton reset = DebouncedButton(RESET_BUTTON_PIN);

EightDigitDisplay display = EightDigitDisplay(LedControl(DISPLAY_DIN_PIN,DISPLAY_CLK_PIN,DISPLAY_CS_PIN,1));

Sensor oxySensor = Sensor(OXY_SENSOR_PIN, 20.95);
Sensor heSensor = Sensor(HE_SENSOR_PIN, 20.95);

Setpoint measuredMix;

MixMenu mixMenu;
bool mixing = false;
bool goodMix = false;

MixSetup mixSetup;

//////////////////////////////////////////////////////////////////
// Basic microcontroller methods

//TODO rebuild with new objects

void setup() {  
  Serial.begin(9600); 
  pinMode(OXY_SENSOR_PIN, INPUT);
  pinMode(HE_SENSOR_PIN, INPUT);

  pinMode(OXY_VALVE_PIN, OUTPUT);
  pinMode(HE_VALVE_PIN, OUTPUT);

  pinMode(ENCODER_SW, INPUT_PULLUP);
  pinMode(RESET_BUTTON_PIN, INPUT_PULLUP);

  delay(1000);
  oxySensor.recalibrate(20.95);
  heSensor.recalibrate(20.95);
  measuredMix.displayDebounce_ = Debouncer(50);
}

void loop() {
#ifdef DEBUGMODE
  debugDisplay();
  delay(1000);
#else
  if (reset.pressed()) {
    mixing = false;
    mixMenu.reset();
    display.clear();
    for (int i = 0; i < 5; ++i) {
      display.writeText("SEnS0r  ", 8);
      delay(500);
      display.writeText("CAL1b   ", 8);
      delay(500);
    }
    oxySensor.recalibrate(20.95);
    heSensor.recalibrate(20.95);
    mixSetup.resetEstimatedMix();
  }
  if(mixing) {
    //TODO add display and PI control of valves
    if(!goodMix) {
      display.writeText("Set Err ", 8);
      mixing = false;
      mixMenu.reset();
    }
    mixSetup.integralControlMix.display(display, 0);
    oxySensor.update();
    heSensor.update();
    measuredMix.computeFromSensors(oxySensor, heSensor);
    mixSetup.updateEstimatedMix(measuredMix);
    mixSetup.updateIntegralControl();
    measuredMix.display(display,1);
  } else {
    mixMenu.display(display);
    mixMenu.getActive().value(encoder.read(mixMenu.getActive().value()));

    if (encoder.button_.pressed()) {
      mixing = mixMenu.next();
    }
    if (mixing) {
      goodMix = mixSetup.updateFromMixMenu(mixMenu);
    }       
  }
#endif
}

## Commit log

2022-11-17 Added first version of hardware design
    [blenderbrain.kicad_pcb, blenderbrain.kicad_sch, freerouting.dsn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]
2022-11-18 Added prototype encoder support
2022-11-19 Added He-Encoder and Oxygen sensor, introduced Machine States
2022-11-20 Changed UI for the first few steps and added a debounced button struct
2022-11-20 Added a simple PID control structure
2022-12-02 Fixed the main methods and deleted some needlessly difficult UI handling
    [main_control_atmega168.ino]
2022-12-03 Fixed encoder bounce by using a state based method
    [main_control_atmega168.ino]
2022-12-03 Added second oxygen sensor to compute the helium content of the mix
2022-12-04 Added MagneticValve and StatusLed classes
2023-03-31 fixed some display issues and added calibration after reset
    [main_controller.ino]
2023-05-26 fixed visualization and reset of estimated mix
    [main_controller.ino]
2023-08-29 feat: added v2 schematic
    [blenderbrain_v2.kicad_sch, freerouting.dsn, temp-freerouting.dsn]
2023-09-01 hardware: added rotary encoder to pcb and made first alignment
    [blenderbrain_v2.kicad_pcb, blenderbrain_v2.kicad_sch]
